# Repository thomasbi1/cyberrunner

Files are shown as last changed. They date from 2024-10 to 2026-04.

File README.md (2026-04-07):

# CyberRunner

CyberRunner (https://youtu.be/zQMKfuWZRdA)

CyberRunner is an AI robot whose task is to learn how to play the popular and widely accessible labyrinth marble game. It is able to beat the best human player with only 6 hours of practice.

This repository contains all necessary code and documentation to build your own CyberRunner robot, and let the robot learn to solve the maze!

**Author: Thomas Bi <br />
With contributions by: Ethan Marot, Tim Flückiger, Cara Koepele, Aswin Ramachandran**

To learn more:
* [Project website](https://cyberrunner.ai)
* [Video](https://youtu.be/zQMKfuWZRdA)
* [Paper](https://arxiv.org/abs/2312.09906)

## Overview

Method

CyberRunner exploits recent advances in model-based reinforcement learning and its ability to make informed decisions about potentially successful behaviors by planning into the future. The robot learns by collecting experience. While playing the game, it captures observations and receives rewards based on its performance, all through the “eyes” of a camera looking down at the labyrinth. A memory is kept of the collected experience. Using this memory, the model-based reinforcement learning algorithm learns how the system behaves, and based on its understanding of the game it recognizes which strategies and behaviors are more promising. Consequently, the way the robot uses the two motors – its “hands” – to play the game is continuously improved. Importantly, the robot does not stop playing to learn; the algorithm runs concurrently with the robot playing the game. As a result, the robot keeps getting better, run after run.

## Documentation

To get started with CyberRunner, please refer to the [Docs](http://cyberrunner.readthedocs.io/).

## Citing
If you use this work in an academic context, please cite the following publication:

* T. Bi, R. D'Andrea,
**"Sample-Efficient Learning to Solve a Real-World Labyrinth Game Using Data-Augmented Model-Based Reinforcement Learning"**, 2024 IEEE International Conference on Robotics and Automation (ICRA). ([PDF](https://arxiv.org/abs/2312.09906))

         @inproceedings{bi2024sample,
          title={Sample-efficient learning to solve a real-world labyrinth game using data-augmented model-based reinforcement learning},
          author={Bi, Thomas and D’Andrea, Raffaello},
          booktitle={2024 IEEE International Conference on Robotics and Automation (ICRA)},
          pages={7455--7460},
          year={2024},
          organization={IEEE}
        }

## License
The source code is released under an [AGPL-3.0 license](LICENSE).

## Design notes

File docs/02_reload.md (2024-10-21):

Reload Mechanism
=====

!!! note

    This page is a work in progress.

> Below are the instructions to add an automatic reload mechanism to the CyberRunner robot. The reload mechanism uses a light sensor to detect when the marble is ready to be reset to the beginning. A solenoid then launches the ball through a tube path back to the start.

## Tools
* Toolkit with Allen wrenches and screwdrivers
* Soldering iron
* Wire clippers and strippers
* Hot glue gun
* Heat gun or hair dryer
* Pliers

## List of Purchased Components
* 1x <a href="https://www.adafruit.com/product/413" target="_blank">Adafruit Large Push-Pull Solenoid</a> 
* 1x <a href="https://store.arduino.cc/products/arduino-nano" target="_blank">Arduino Nano</a>
* 1x <a href="https://www.adafruit.com/product/4681" target="_blank"> Adafruit BH1750 Light Sensor</a>
* 1x <a href="https://www.pololu.com/product/2804" target="_blank">Polulu RC Relay Switch</a>
* 1x <a href="https://www.galaxus.ch/en/s14/product/lumina-swiss-power-supply-dc24v-3a-lighting-accessories-21674974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" target="_blank">DC 24V 3A Power Supply</a> (Example)
* 1x White LED
* 1x 330 Ohm Resistor
* <a href="https://www.adafruit.com/product/793" target="_blank">F/F Jumper Cables</a> (Example)
* 9x M3x8 bolts 
* 6x M3x12 bolts
* 4x M2x16 bolts
* 4x M2 nuts
* Heat shrink
* Optional: Barrel jack adapter to power the solenoid

## List of 3D-Printed Components
* 4x <a href="https://github.com/thomasbi1/cyberrunner/blob/master/docs/assets/reload/reload_leg.step" target="_blank">Labyrinth Legs</a> 
* 1x <a href="https://github.com/thomasbi1/cyberrunner/blob/master/docs/assets/reload/reload_solenoid_push_head.step" target="_blank">Solenoid Push Head Cover</a>
* 1x <a href="https://github.com/thomasbi1/cyberrunner/blob/master/docs/assets/reload/solenoid_sensor_mount.step" target="_blank">Reload Marble Tray - Part 1</a> 
* 1x <a href="https://github.com/thomasbi1/cyberrunner/blob/master/docs/assets/reload/reload_sensor_cover_2.step" target="_blank">Sensor Cover - Part 2</a> 
* 1x <a href="https://github.com/thomasbi1/cyberrunner/blob/master/docs/assets/reload/reload_corridor_3.step" target="_blank">Corridor after Solenoid - Part 3</a> 
* 1x <a href="https://github.com/thomasbi1/cyberrunner/blob/master/docs/assets/reload/reload_corridor_4.step" target="_blank">Corridor - Part 4</a> 
* 1x <a href="https://github.com/thomasbi1/cyberrunner/blob/master/docs/assets/reload/reload_corridor_5.step" target="_blank">Corridor - Part 5</a> 
* 1x <a href="https://github.com/thomasbi1/cyberrunner/blob/master/docs/assets/reload/reload_4_5_mount_6.step" target="_blank">Corridor Mount between 4 and 5 - Part 6</a> 
* 1x <a href="https://github.com/thomasbi1/cyberrunner/blob/master/docs/assets/reload/reload_corridor_7.step" target="_blank">Corridor - Part 7</a> 
* 1x <a href="https://github.com/thomasbi1/cyberrunner/blob/master/docs/assets/reload/reload_corridor_8.step" target="_blank">Corridor - Part 8</a> 
* 1x <a href="https://github.com/thomasbi1/cyberrunner/blob/master/docs/assets/reload/reload_7_8_mount_9.step" target="_blank">Corridor Mount between 7 and 8 - Part 9</a> 
* 1x <a href="https://github.com/thomasbi1/cyberrunner/blob/master/docs/assets/reload/reload_end_holder.step" target="_blank">Corridor End Mount</a> 
* 1x <a href="https://github.com/thomasbi1/cyberrunner/blob/master/docs/assets/reload/reload_corner_holder.step" target="_blank">Corridor Corner Mount</a>
* 1x <a href="https://github.com/thomasbi1/cyberrunner/blob/master/docs/assets/reload/reload_electronics_mount.step" target="_blank">Electronics Holder</a> 

## Building the Reload Mechanism

1. Remove the marble tray. 
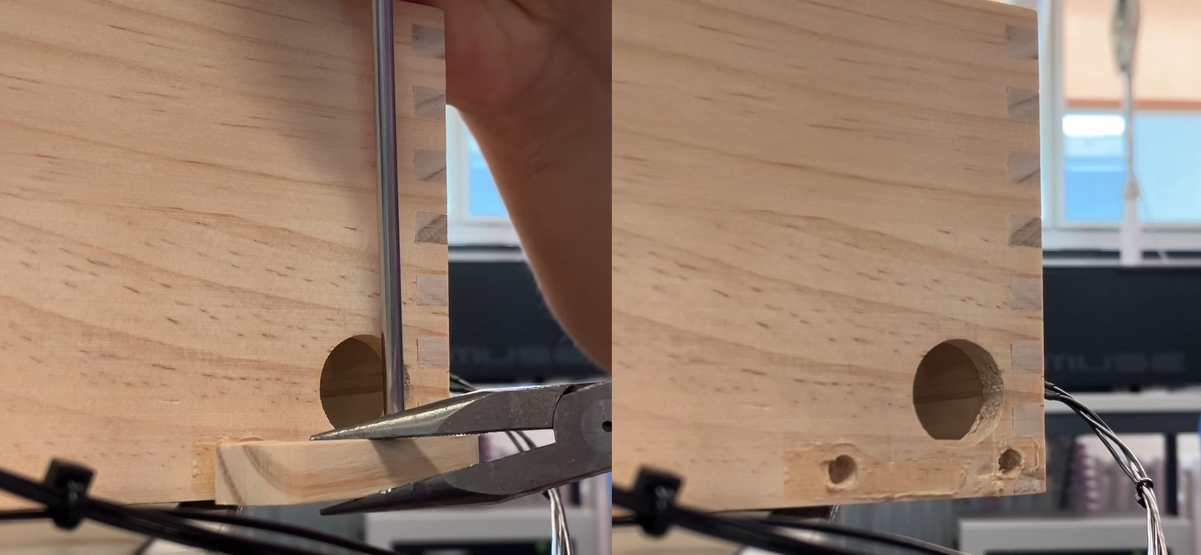
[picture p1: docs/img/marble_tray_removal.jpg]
marble_tray

<br><br>

2. Install the legs on each corner of the labyrinth.

3. Start assembling the new marble tray, which houses the LED, light sensor, and solenoid. Begin with the light sensor and LED wiring. 
    - Solder the pins onto the light sensor PCB facing away from the light sensor. **(Note: This is opposite to the direction shown in the photo)**
    - Solder a 330 Ohm resistor to a (shortened) power lead of the white LED. Solder the other end of the resistor to a female jumper cable. This will connect to the light sensor PCB for power.
    - Create a grounding cable that splits from the (shortened) ground lead of the LED to two female jumper cables. These cables will connect to ground pins on the light sensor PCB and the Arduino.
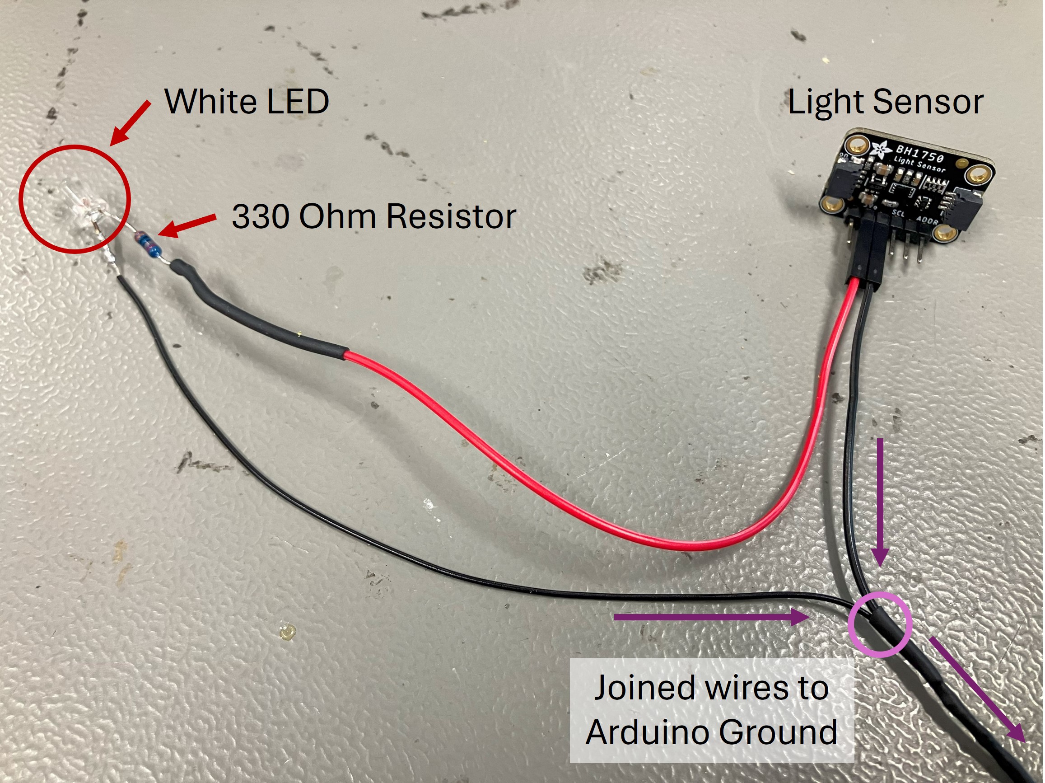
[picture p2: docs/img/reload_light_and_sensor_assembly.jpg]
light_sensor

<br><br>

4. Insert the LED into the designated hole in the printed marble tray. Bend its wires carefully along the corridor so they do not touch each other. Hot glue the wires and the LED in place.<!-- ![knobs](img/marble_tray_removal.jpg) -->
<br><br>

5. Insert the light sensor into its designated spot on the printed marble tray opposite the LED. Install the sensor cover (Part 2).<!-- ![knobs](img/marble_tray_removal.jpg) -->
<br><br>

6. Put the printed cap on the solenoid piston. Attach the solenoid to the printed marble tray using four M3x12 bolts. Ensure the piston faces inward to launch the marble.<!-- ![knobs](img/marble_tray_removal.jpg) -->
<br><br>

7. Secure the reload mechanism assembly to the labyrinth with two M3x8 bolts in the lower right holes of the connection points. <!-- ![knobs](img/marble_tray_removal.jpg) -->
<br><br>

8. Assemble the marble return corridor using the numbered parts:
    - Press-fit Part 3 into the printed marble tray and secure it to the labyrinth with one 3Mx8 bolt. Attach Part 4 to Part 3. 
    - Connect Parts 4 and 5 using Part 6, securing it to the top of the labyrinth with two 3Mx8 bolts. 
    - Press-fit Part 7 to Part 5. Connect Part 7 and Part 8 with Part 9. Secure Part 9 to the top of the labyrinth with two 3Mx8 bolts. 
    - Attach the end mount to Part 8 and secure it above the maze start with two 3Mx8 bolts. 
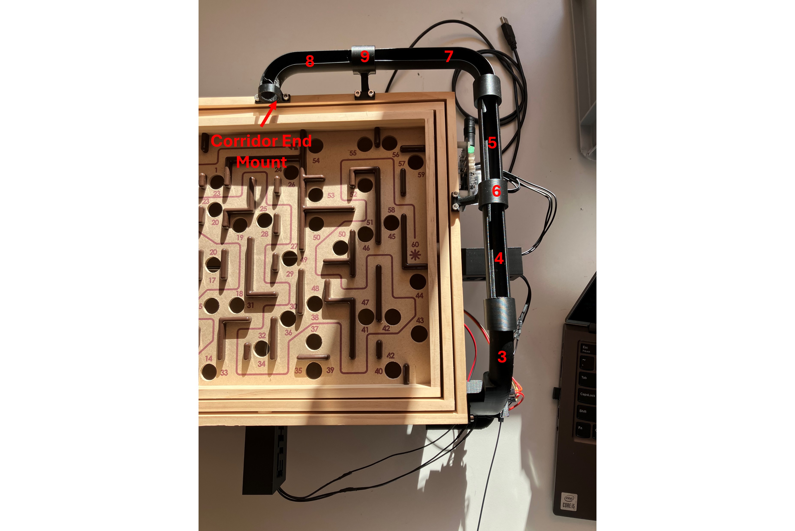
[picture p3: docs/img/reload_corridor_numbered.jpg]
reload_corridor

<br><br>

9. Connect the cables for the light sensor, solenoid, Arduino, and relay according to the wiring diagram. Optionally, connect the solenoid and relay to the 24V power supply using a barrel jack connector in the electronics housing. 
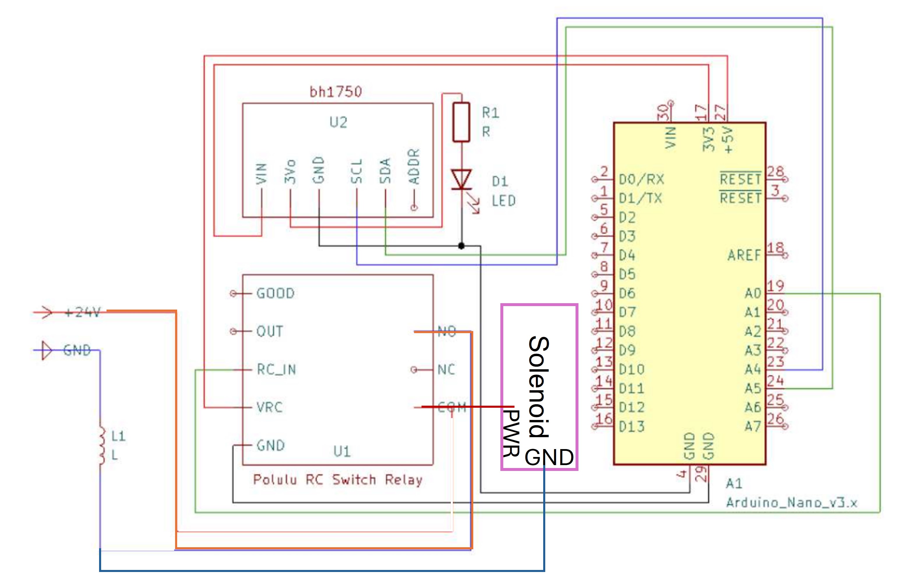
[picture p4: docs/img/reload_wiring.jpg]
reload_wiring

<br><br>

10. Secure the relay in the electronics housing with M2x16 bolts and nuts. Press-fit the Arduino in the leg features. 
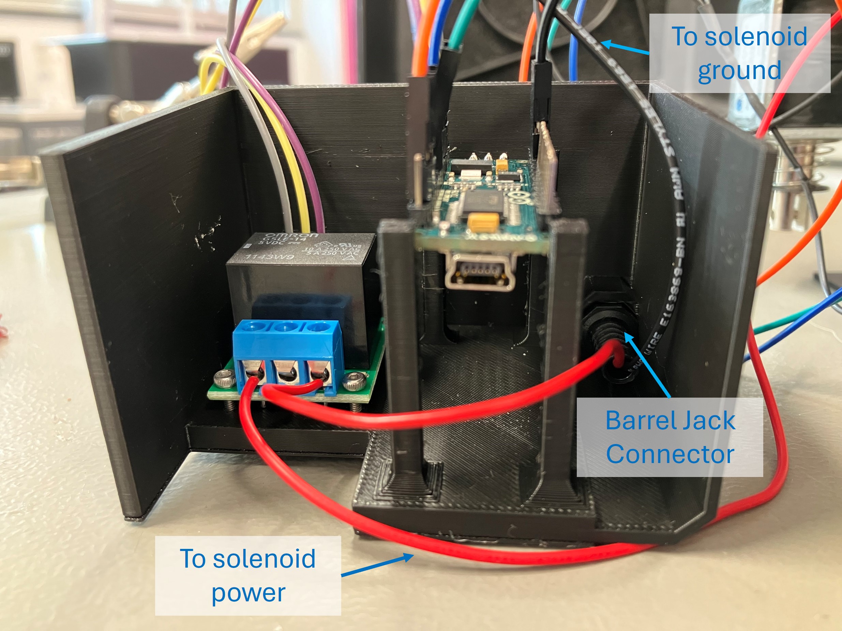
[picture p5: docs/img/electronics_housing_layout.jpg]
housing_layout

<br><br>

11. Attach the housing to the labyrinth with two M3x12 bolts.
<br><br>

## Configuring the Electronics

1. Plug in the Arduino to your PC and upload <a href="https://github.com/thomasbi1/cyberrunner/blob/master/docs/assets/reload/arduino/main.ino" target="_blank">this script</a> to the Arduino Nano. Ensure that the BH1750 library is installed.

2. If the Arduino is powered, you should hear the relay respond when the LED is blocked by the marble. Power the solenoid with the 24V power supply to engage the reload feature!

 <!-- and (2) every 10 minutes without sensor detection. The latter response attempts to jiggle out stuck marbles from the labyrinth. -->

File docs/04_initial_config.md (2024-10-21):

Initial Configuration
=====

Before we can start using CyberRunner, we need to first **calibrate the camera** and **configure the motors**. These steps have to be taken only once. 

## Camera Calibration

In order for the position of the ball within the labyrinth to be tracked, we need to first calibrate the camera. For this purpose, we use the <a href="https://sites.google.com/site/scarabotix/ocamcalib-omnidirectional-camera-calibration-toolbox-for-matlab" target="_blank">COCamCalib MATLAB toolbox</a>.

1. Follow the steps <a href="https://sites.google.com/site/scarabotix/ocamcalib-omnidirectional-camera-calibration-toolbox-for-matlab" target="_blank">here</a> to obtain the calibration results for your camera. 

    !!! warning "Disclaimer"

        The **Find Center** step is computationally intensive and may get stuck. In this case, update `PP` in both instances of the function `lsqlin()` to `sparse(PP)`. This should speed up the process. For more details, the bug fix is idenitified in <a href="https://groups.google.com/g/ocamcalib-toolbox/c/ZgVP4LHd-6w?pli=1" target="_blank">this thread</a>.

    Make sure to take the calibration pictures at a 1920x1200 resolution.

2. Save the calibration results by clicking on **Export Data** in the OCamCalib GUI. This will create the file `calib_results.txt` in your MATLAB workspace.

3. Copy the `calib_results.txt` file as `calib_results_cyberrunner.txt` to your ROS workspace with

        cp <path_to_matlab_workspace>/calib_results.txt <path_to_cyberrunner_ws>/src/cyberrunner/cyberrunner_state_estimation/calib/calib_results_cyberrunner.txt
    Replace `<path_to_matlab_workspace>` and `<path_to_cyberrunner_ws>` with the path to your MATLAB workspace and your CyberRunner ROS workspace, respectively.

4. Install the calibration file by navigating to your workspace and running

        colcon build --symlink-install
        source install/setup.bash

## Marker positions

The state estimator relies on approximately knowing the location of the blue markers within the image. To obtain these positions follow these steps.

1. Open two terminal windows, navigate to the CyberRunner workspace and source the workspace.

2. In the first terminal, run the camera script

        ros2 run cyberrunner_camera cam_publisher.py

3. In the second terminal, run the select markers script and follow the instructions in the terminal

        ros2 run cyberrunner_state_estimation select_markers

## Motor Configuration

1. Install [Dynamixel Wizard 2.0](https://emanual.robotis.com/docs/en/software/dynamixel/dynamixel_wizard2/).
2. Temporarily disconnect the front motor (the motor on the longer side of the labyrinth). Connect the U2D2 to your host PC and ensure that the motors are turned on by pressing the power switch on the U2D2 Power Hub Board.
3. In the Dynamixel Wizard, press **Scan** until the motor is found.
4. Assign **ID 2** to the connected motor, set the baud rate to 1M, and set the operating mode to 0 (Current Control Mode). Make sure to click **Save** after each change.
5. Reconnect the front motor.
6. Press **Scan** again.
7. For the newly connected motor, assign **ID 1**, and apply the same changes as for the other motor.

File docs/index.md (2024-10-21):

# CyberRunner Documentation

Welcome to the CyberRunner docs! Here you'll find tutorials and other useful information to get you started with CyberRunner.

## Requirements

* Ubuntu 22.04
* MATLAB
* GPU: min. 1x RTX 2080 Super

## Tutorials

* [Hardware Setup](01_hardware_setup.md): Build your own CyberRunner robot.
* [Reload Mechanism](02_reload.md): Add an automatic reload mechanism to your CyberRunner robot.
* [Installation](03_installation.md): Install all necessary dependencies and the CyberRunner software stack.
* [Initial Configuration](04_initial_config.md): Calibrate the camera and configure the motors.
* [Train](05_train.md): Let CyberRunner learn to play the labyrinth game.
* [Troubleshooting](06_troubleshooting.md): Fix common issues.

!!! note "Note"

    This project is under active development.

<!-- !!! Potential addition

    Video tutorials? This applies to software and configuration as well -->

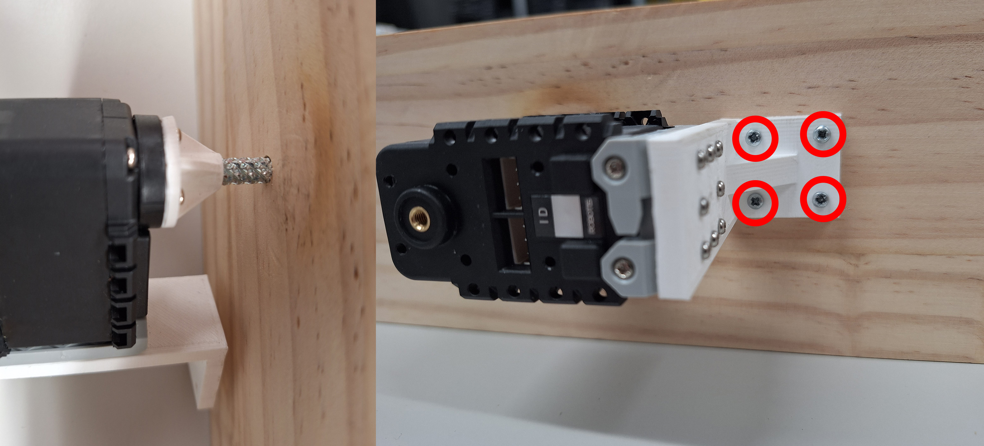
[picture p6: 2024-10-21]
docs/img/motorfix.jpg

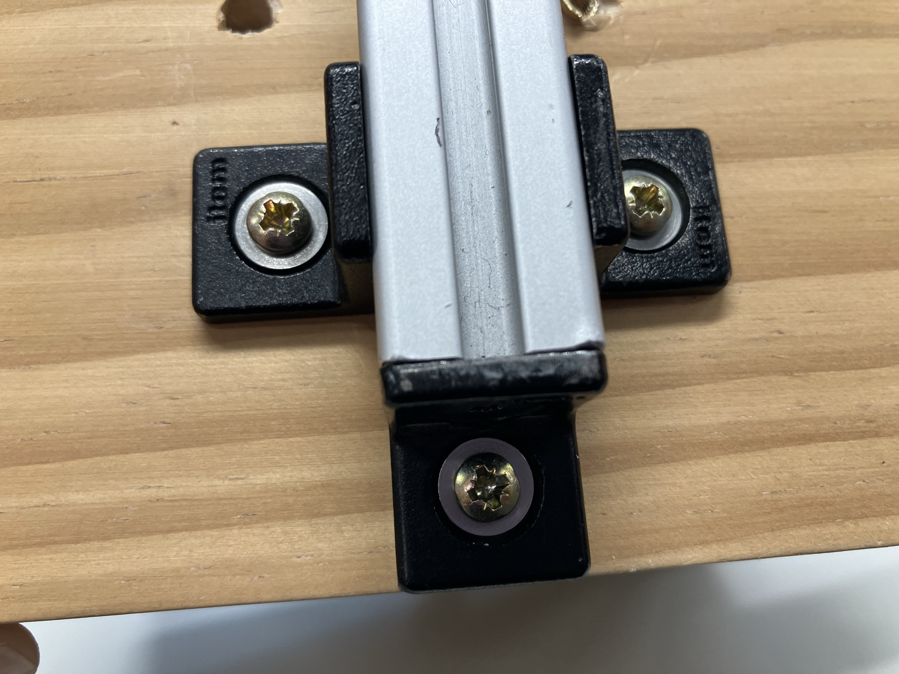
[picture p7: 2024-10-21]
docs/img/camera_scaffolding_to_labyrinth.jpg

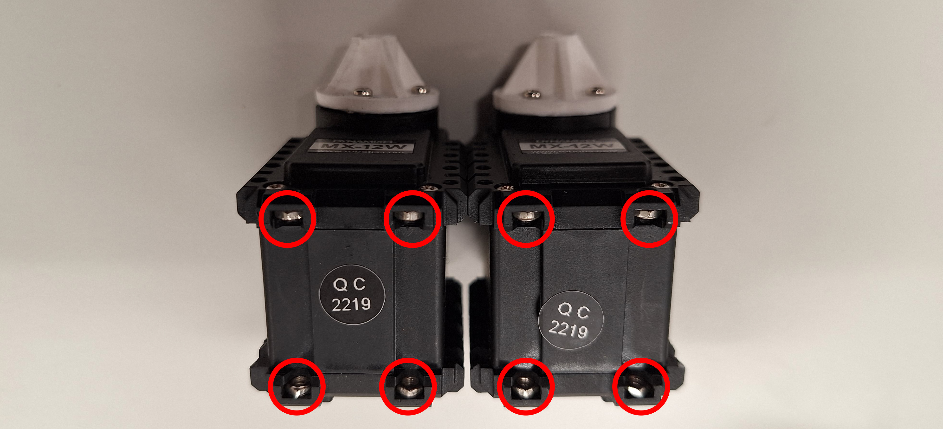
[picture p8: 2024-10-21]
docs/img/nuts.jpg

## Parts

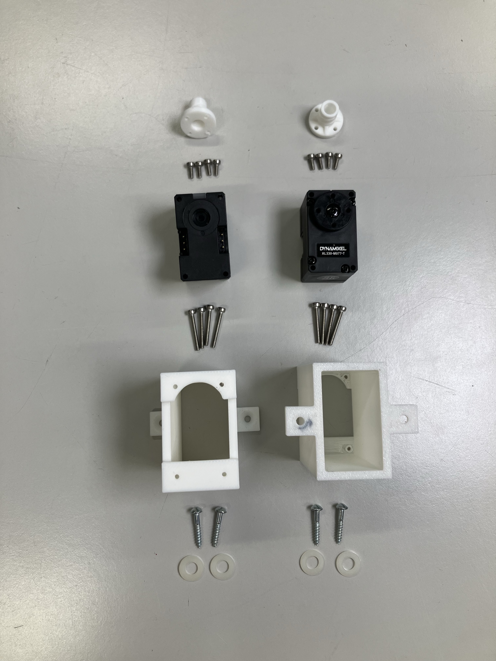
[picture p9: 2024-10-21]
docs/img/motor_housing_parts.jpg

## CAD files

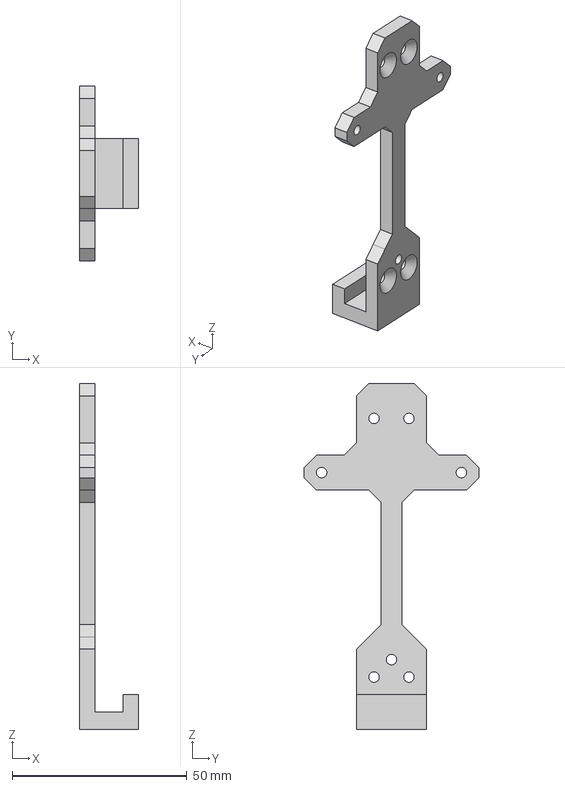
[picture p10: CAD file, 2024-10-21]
docs/assets/camera/camera_assembly_mount.step
17.0 x 50.0 x 99.0 mm

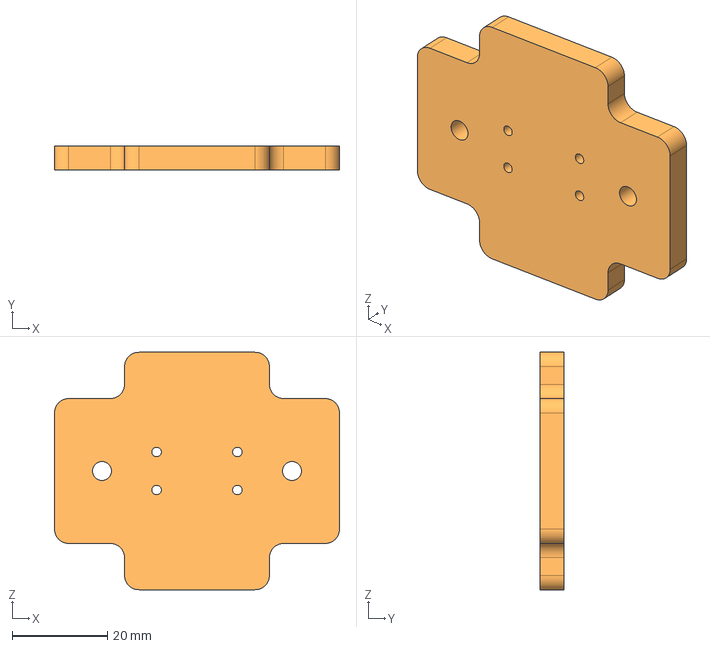
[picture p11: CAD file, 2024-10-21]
docs/assets/camera/camera_mounting_plate.step
60.0 x 5.00 x 50.0 mm

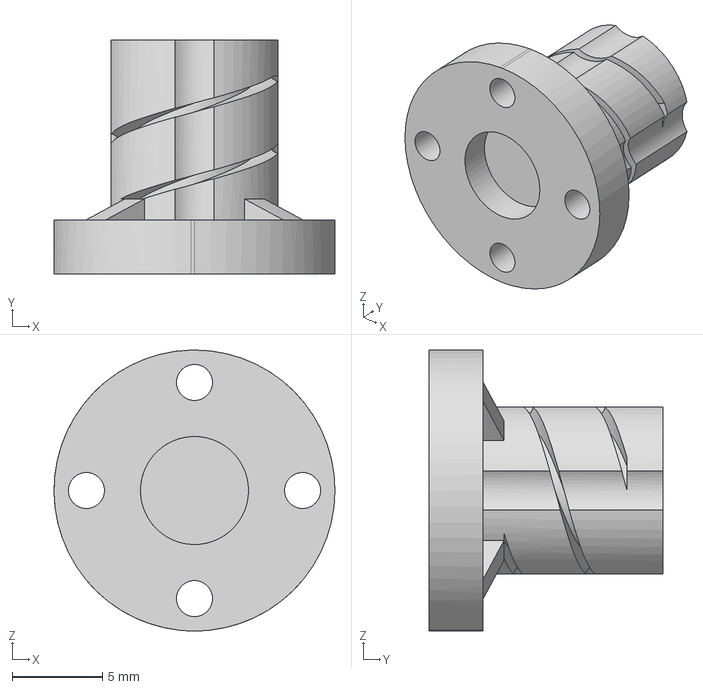
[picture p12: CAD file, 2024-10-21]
docs/assets/motors/motor_shaft_coupler.step
15.6 x 13.0 x 15.6 mm

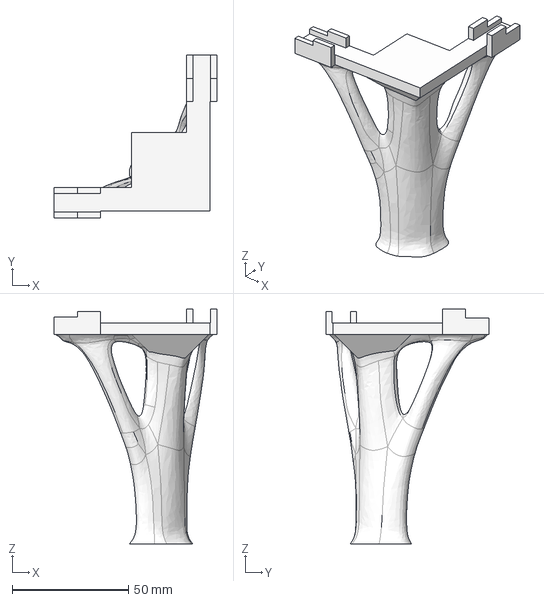
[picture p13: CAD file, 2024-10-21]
docs/assets/reload/reload_leg.step
70.0 x 70.0 x 101.0 mm

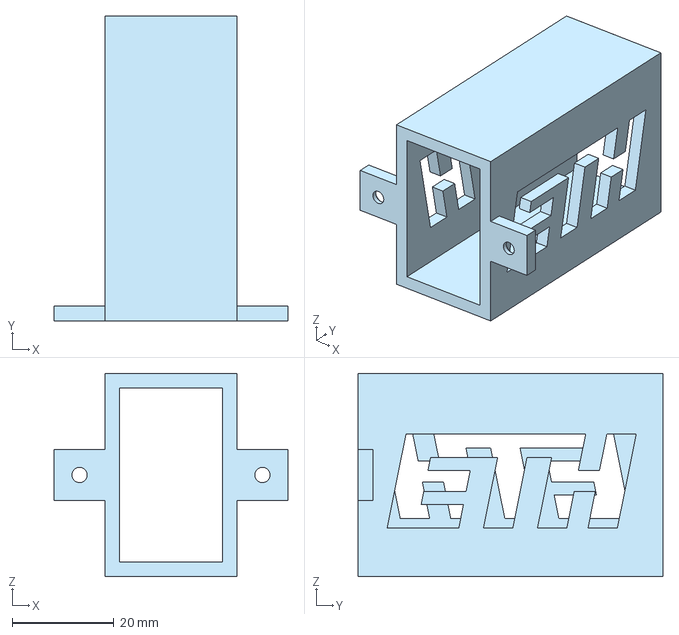
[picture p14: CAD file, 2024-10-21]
docs/assets/motors/motor_mounting_bracket.step
46.0 x 60.0 x 40.0 mm

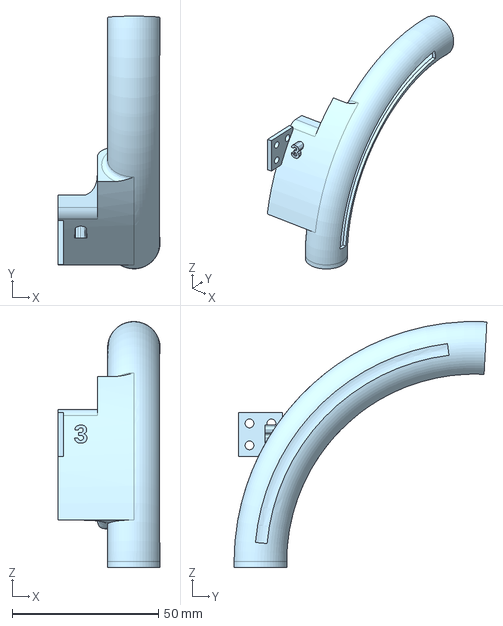
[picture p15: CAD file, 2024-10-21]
docs/assets/reload/reload_corridor_3.step
35.0 x 86.4 x 84.1 mm

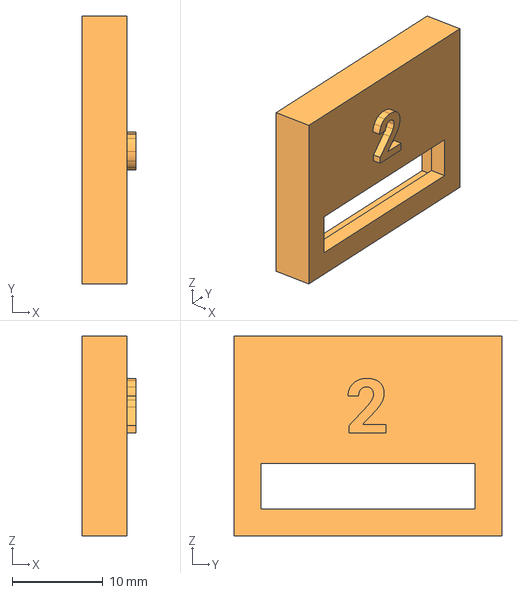
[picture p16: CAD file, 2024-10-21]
docs/assets/reload/reload_sensor_cover_2.step
6.00 x 29.6 x 22.1 mm

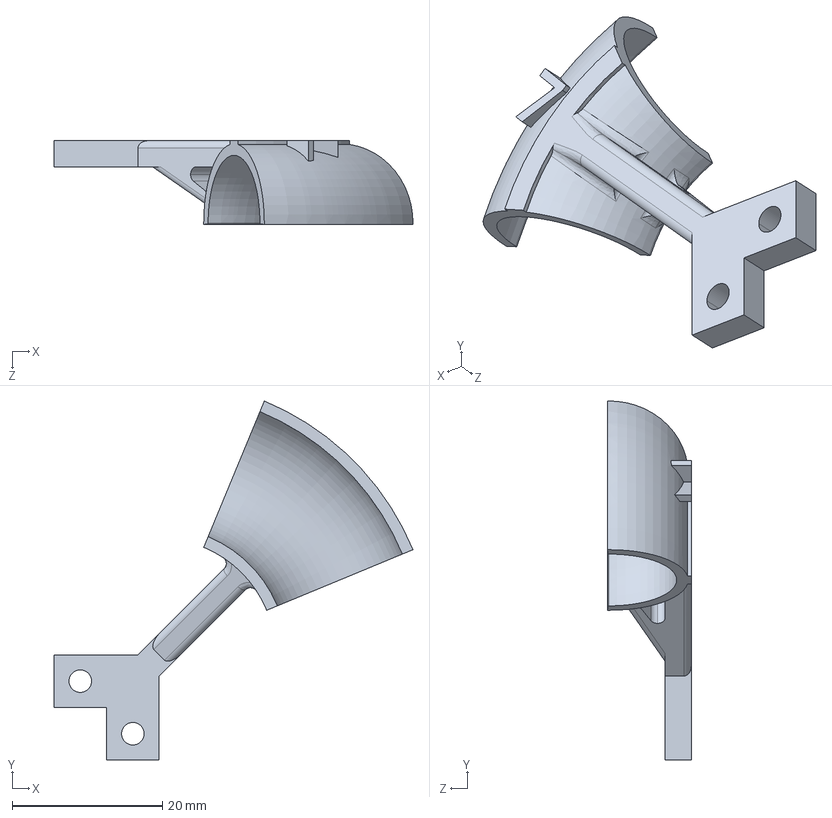
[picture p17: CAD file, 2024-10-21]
docs/assets/reload/reload_corner_holder.step
47.8 x 47.8 x 11.1 mm

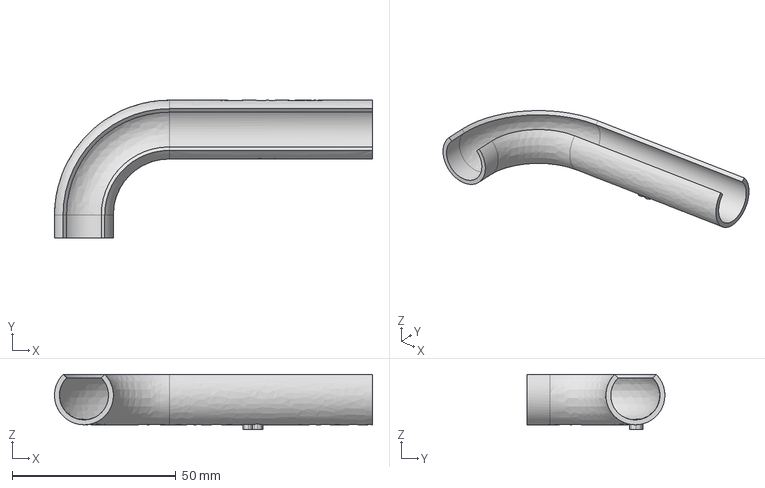
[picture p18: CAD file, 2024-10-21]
docs/assets/reload/reload_corridor_8.step
97.0 x 42.0 x 16.8 mm

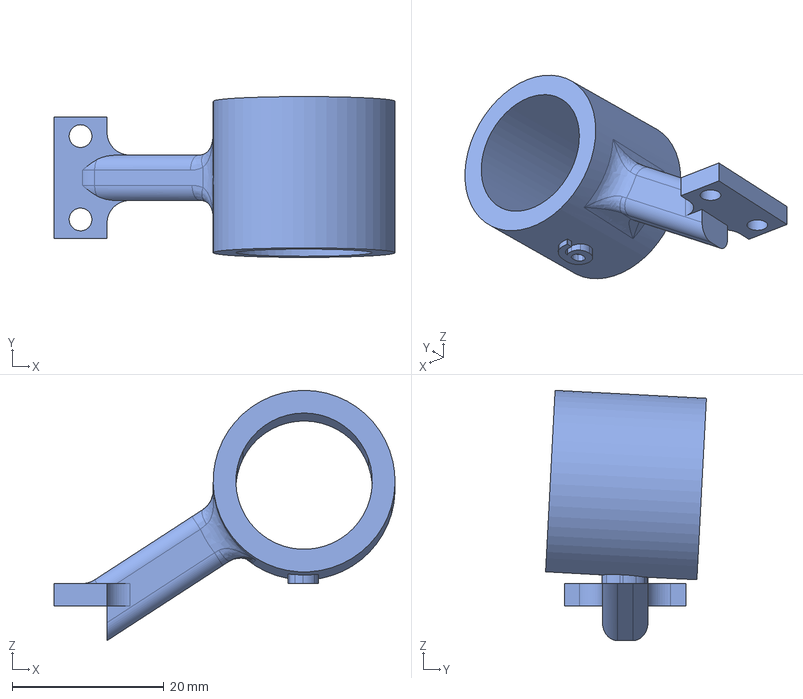
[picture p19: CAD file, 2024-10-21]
docs/assets/reload/reload_4_5_mount_6.step
45.0 x 21.2 x 33.0 mm

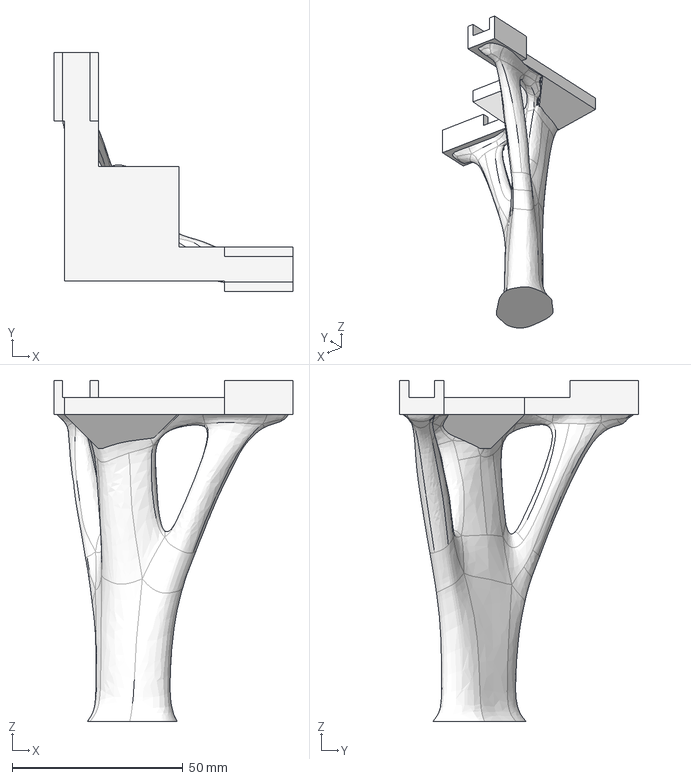
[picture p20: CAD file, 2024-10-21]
docs/assets/reload/reload_leg_electronics.step
70.0 x 70.0 x 100.0 mm

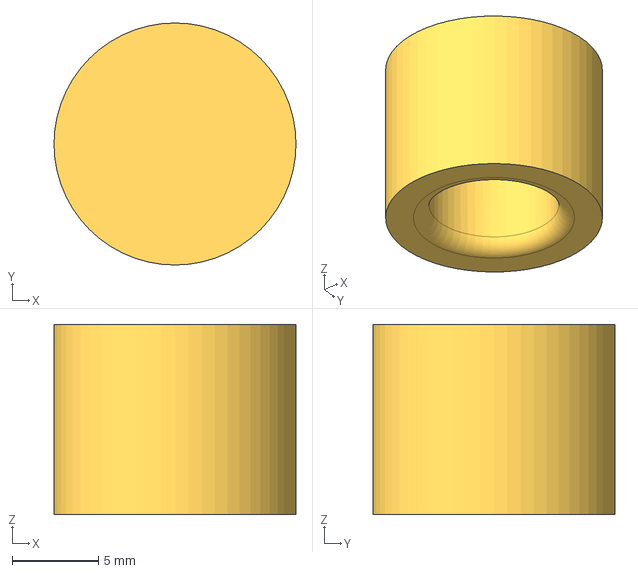
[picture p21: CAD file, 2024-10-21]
docs/assets/reload/reload_solenoid_push_head.step
14.0 x 14.0 x 11.0 mm

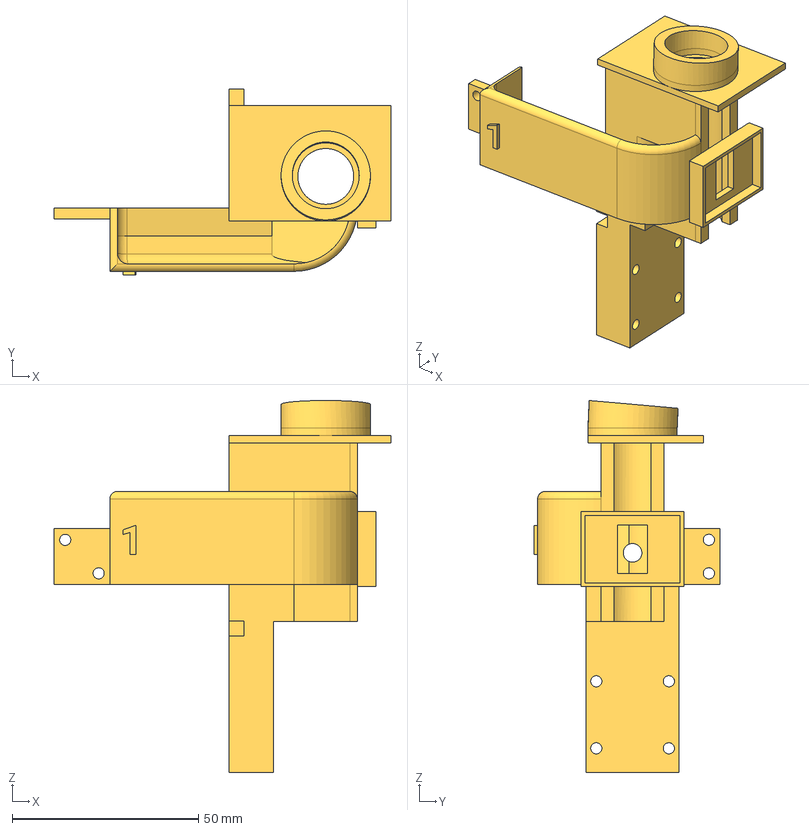
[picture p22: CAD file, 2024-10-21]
docs/assets/reload/solenoid_sensor_mount.step
90.5 x 50.0 x 99.9 mm

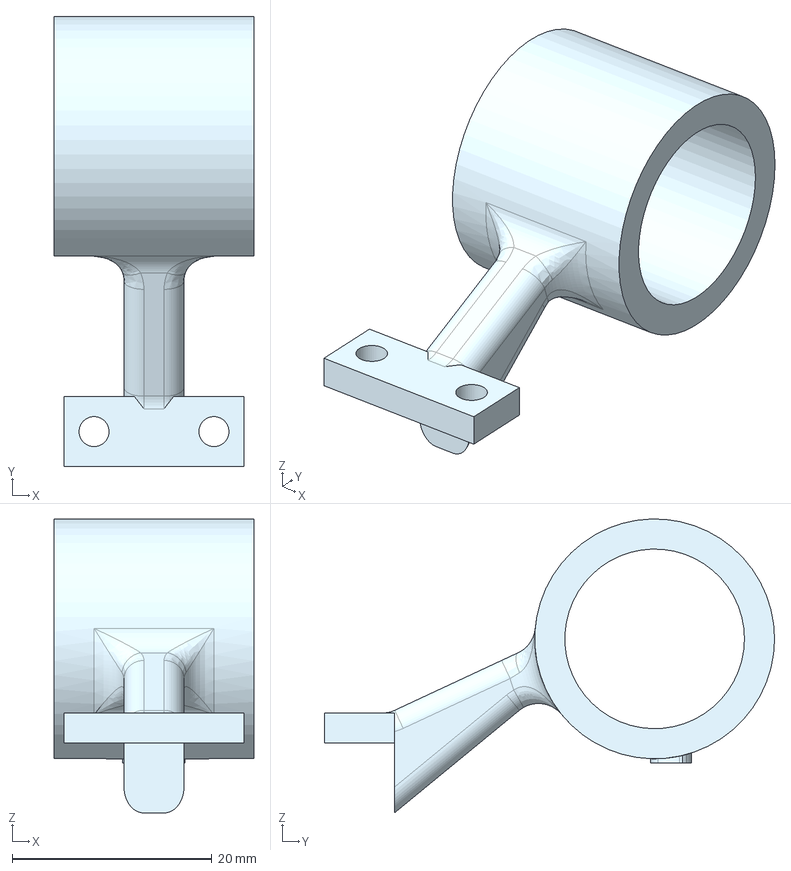
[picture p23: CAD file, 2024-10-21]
docs/assets/reload/reload_7_8_mount_9.step
20.0 x 45.0 x 29.4 mm

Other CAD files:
docs/assets/reload/reload_corridor_4.step
docs/assets/reload/reload_end_holder.step
docs/assets/reload/reload_corridor_5.step
docs/assets/reload/reload_corridor_7.step
docs/assets/reload/reload_brightness_cover.step
docs/assets/reload/reload_electronics_mount.step

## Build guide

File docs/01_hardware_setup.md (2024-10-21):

Hardware Setup
=====

## List of Components

### Tools
* 3D-Printer access and PLC filament (Tested with Bambu X1E)
* Toolkit with Allen wrenches, screwdrivers, and a handheld drill
* Wire cutters and strippers
* Soldering iron
* Heat gun or hair dryer
* Pliers

### Labyrinth
<!-- * 1x [BRIO Labyrinth](https://www.brio.us/en-US/products/games/labyrinth-game-63400000) (wooden version) -->
* 1x <a href="https://www.brio.us/en-US/products/games/labyrinth-game-63400000" target="_blank">BRIO Labyrinth</a> (wooden version)

### XL330-M077-T Motors 
* 2x <a href="https://www.robotis.us/dynamixel-xl330-m077-t/" target="_blank">ROBOTIS Dynamixel XL330-M077-T</a>
* 1x <a href="https://www.robotis.us/u2d2/" target="_blank">ROBOTIS U2D2</a>
* 1x <a href="https://www.robotis.us/u2d2-power-hub-board-set/" target="_blank">ROBOTIS U2D2 Power Hub Board</a>
* 3x wires to extend cable to reach between both motors
* 1x 5V3A Power Supply (2.5mm ID / 5.5mm OD) - <a href="https://www.amazon.com/Supply-Adapter-100-240V-Replacement-Transformer/dp/B0B524GZMN" target="_blank">example</a>
* 2x <a href="https://github.com/thomasbi1/cyberrunner/blob/master/docs/assets/motors/motor_shaft_coupler.step" target="_blank">Motor couplings</a> (to 3d print)
    Note: These couplings may break after being coupled to the motor. We recommend to print 2x extra.
* 2x <a href="https://github.com/thomasbi1/cyberrunner/blob/master/docs/assets/motors/motor_mounting_bracket.step" target="_blank">Motor mounting brackets</a> (to 3d print)
* 8x M2x6 B610 bolts fix couplers to the motors (included with motors)
* 4x M3x10 bolts to mount bracket to the labyrinth
* Heat shrink

### Camera
* 1x <a href="https://www.e-consystems.com/industrial-cameras/ar0234-usb3-global-shutter-camera.asp#" target="_blank">See3CAM_24CUG USB3 Camera</a> (with enclosure)
* 1x <a href="https://github.com/thomasbi1/cyberrunner/blob/master/docs/assets/camera/camera_mounting_plate.step" target="_blank">Camera mounting plate</a> 
* 1x <a href="https://github.com/thomasbi1/cyberrunner/blob/master/docs/assets/camera/camera_assembly_mount.step" target="_blank">Camera assembly bracket</a>
* 4x M2x8 bolts to attach the camera to the mounting plate
* 2x 2020 T-slotted Aluminum with lengths of 40 cm and 20 cm
* 7x L-brackets for T-slotted aluminum, size M5
* 9x T-slot nuts, size M5
* 9x T-slot bolts, size M5x8
* 2x T-slot bolts, size M4x10, to attach the mounting plate to the L-brackets
* 4x M2.5x10 bolts to attach the assembly bracket to the labyrinth
* 3x M3x8 bolts to mount the camera assembly to the bracket on the labyrinth
* 3x M3 washers to sit between the bolts and the L-brackets that attach to the assembly bracket

!!! note "Information"
    One of the ends of the 40 cm T-slotted aluminum parts needs to be tapped for an M5 bolt. 

### Miscellaneous
* 8x <a href="https://www.herma.co.uk/office-home/product/colour-dots-small-pack-1833/" target="_blank">Dark blue circle labels</a> (8mm diameter)
* 1x <a href="https://www.amazon.com/Ravensburger-27468-GraviTrax-Ball-Box/dp/B0BSX781QZ" target="_blank">Blue colored marbles</a>

## Building CyberRunner

###  XL330-M077-T Motors

1. Using a flathead screwdriver, carefully pry the two knobs off of the labyrinth. Applying heat to the knobs with a heat gun or hair dryer will facilitate this process.
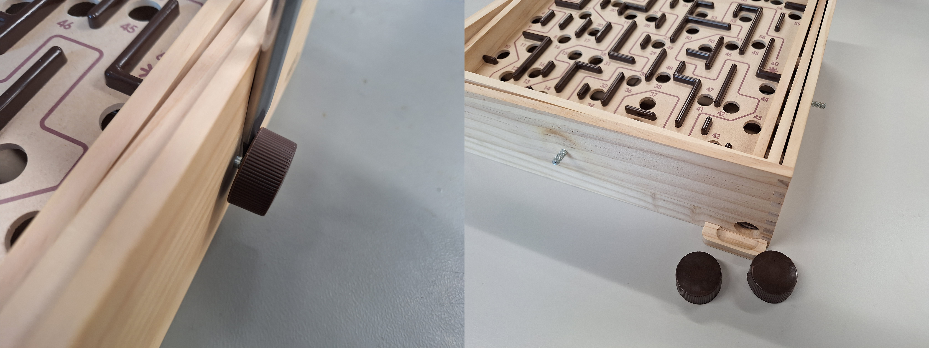
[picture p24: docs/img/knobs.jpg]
knobs

<br><br>

2. Secure the motor couplers to the motors using the provided M2x6 bolts.
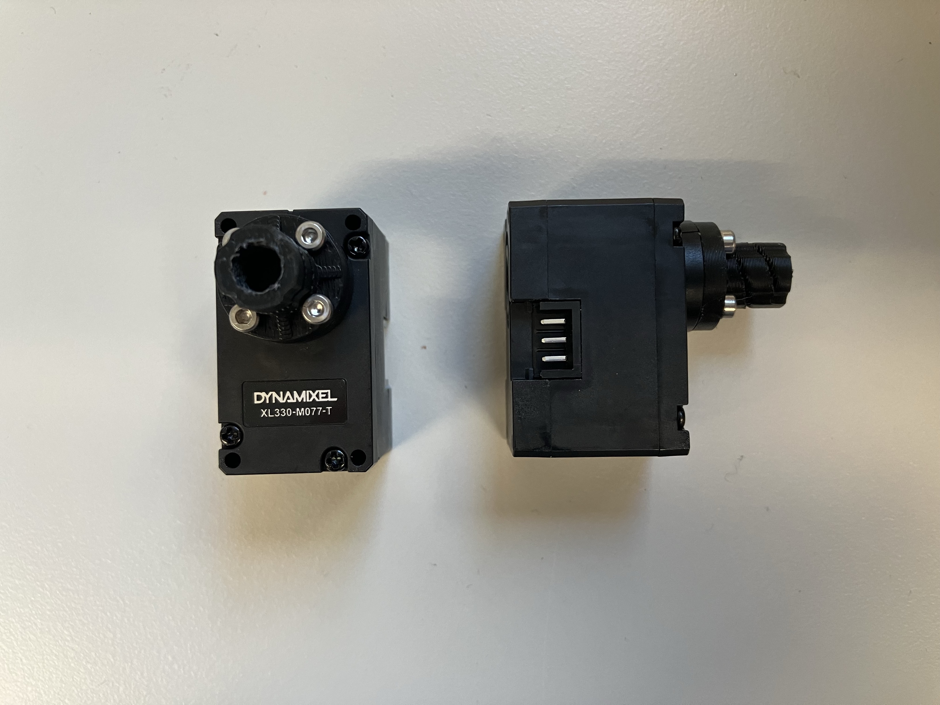
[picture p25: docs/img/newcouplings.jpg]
newcouplers

<br><br>

3. Drill pilot holes on the labyrinth to prepare for the installation of the motor housings. 
<br><br>

4. Connect the motors to the labyrinth shafts. If necessary, slightly heat the couplers with a heat gun or hair dryer to assist with the fitting. Slide the 3D-printed housings over the motors and secure the motor housings to the labyrinth with the M3x10 bolts.
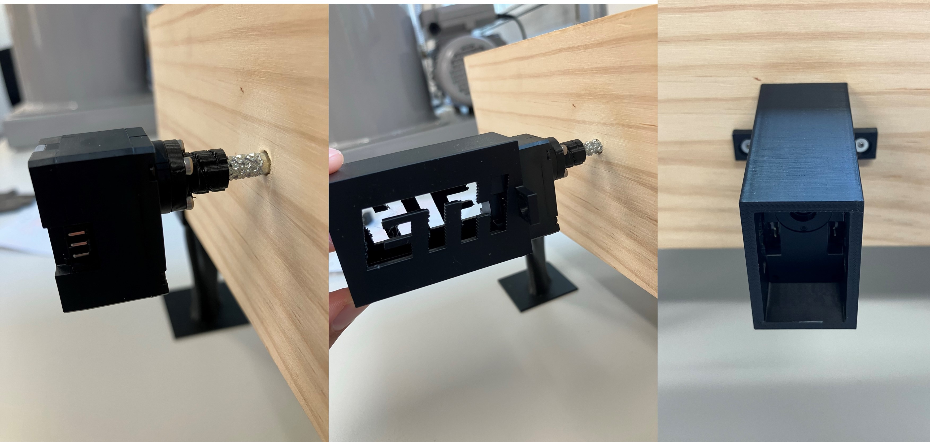
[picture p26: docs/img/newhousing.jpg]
newnuts

<br><br>

<!-- ###  MX-12W Motors (Option 2)

!!! warning "Disclaimer"

    The Dynamixel MX-12W motors have been discontinued. Instructions for the Dynamizel XL330-M077-T motors are above.

1. Carefully remove the two knobs from the labyrinth by using a flathead screwdriver and pressing the knobs away from the labyrinth board. Slightly heating the knobs with a heat gun or a hairdryer will facilitate this process.
![knobs](img/knobs.jpg)
<br><br>

2. Mount the motor couplers to the front of the motors using the M2x6 bolts included with the motors.
![couplers](img/couplers.jpg)
<br><br>

3. Insert the included nuts on the underside of the motors.
![nuts](img/nuts.jpg)
<br><br>

4. Mount the included mounting frames of the motors to the 3d-printed mounting brackets using the included M2x6 bolts and nuts.
![brackets](img/brackets.jpg)
<br><br>

5. Attach the motors to the mounting frames using the included M2x6 bolts.
![motorframe](img/motorframe.jpg)
<br><br>

6. Press both motor couplers over the labyrinth shafts. You may need to slightly heat the couplers with a heat gun or hairdryer. Then, fix the motors to the labyrinth by using the M2.5x10 wood screws.
![motorfix](img/motorfix.jpg) -->

### Camera

The camera has to be have a stable view of the whole labyrinth. This can be done with a scaffolding made with 2020 T-slotted Aluminum and a 3D-Printed camera mounting plate as described below.
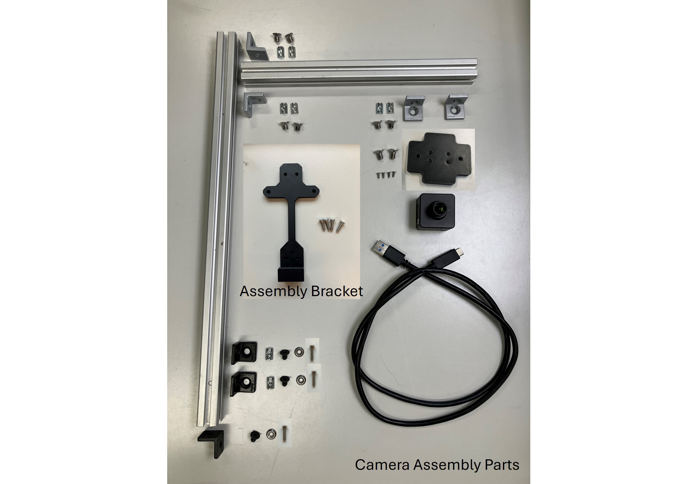
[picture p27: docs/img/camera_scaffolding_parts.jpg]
cameraparts


1. Tap one end of the 40 cm T-slotted aluminum to fit a M5 bolt. Mount the camera to the mounting plate with four M2x8 bolts and assmble the aluminum profiles as shown in the picture.  
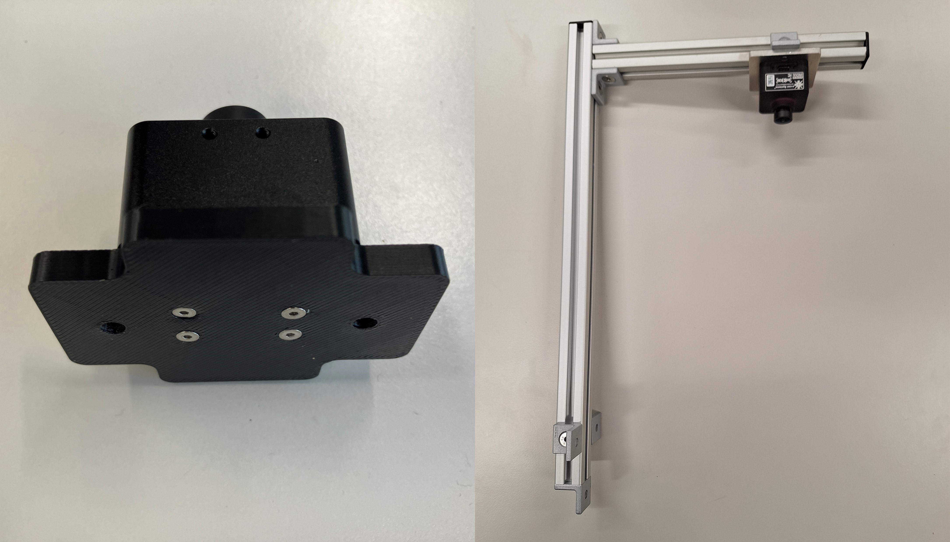
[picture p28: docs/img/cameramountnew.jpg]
cameramount

<br><br>

2. Secure the camera assembly bracket to the labyrinth using four M2.5x10 bolts. Ensure that the bracket is centered. Note that the shaft for the knob on the opposite end is not centered with respect to the playing area.
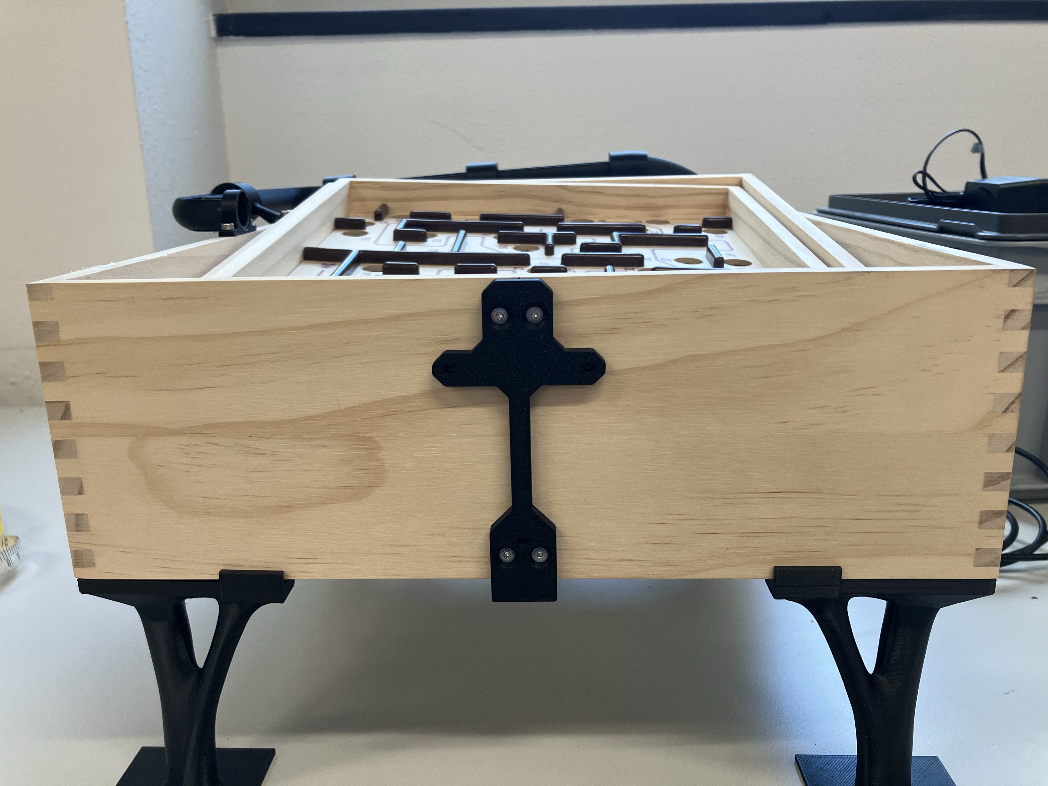
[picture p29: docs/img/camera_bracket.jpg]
camerabracket

<br><br>

3. Mount the camera assembly to the labyrinth board using three M3x8 bolts and M3 washers. Adjust the height of the camera so the distance between the bottom of the lens and the labyrinth playing area is approximately 25cm.
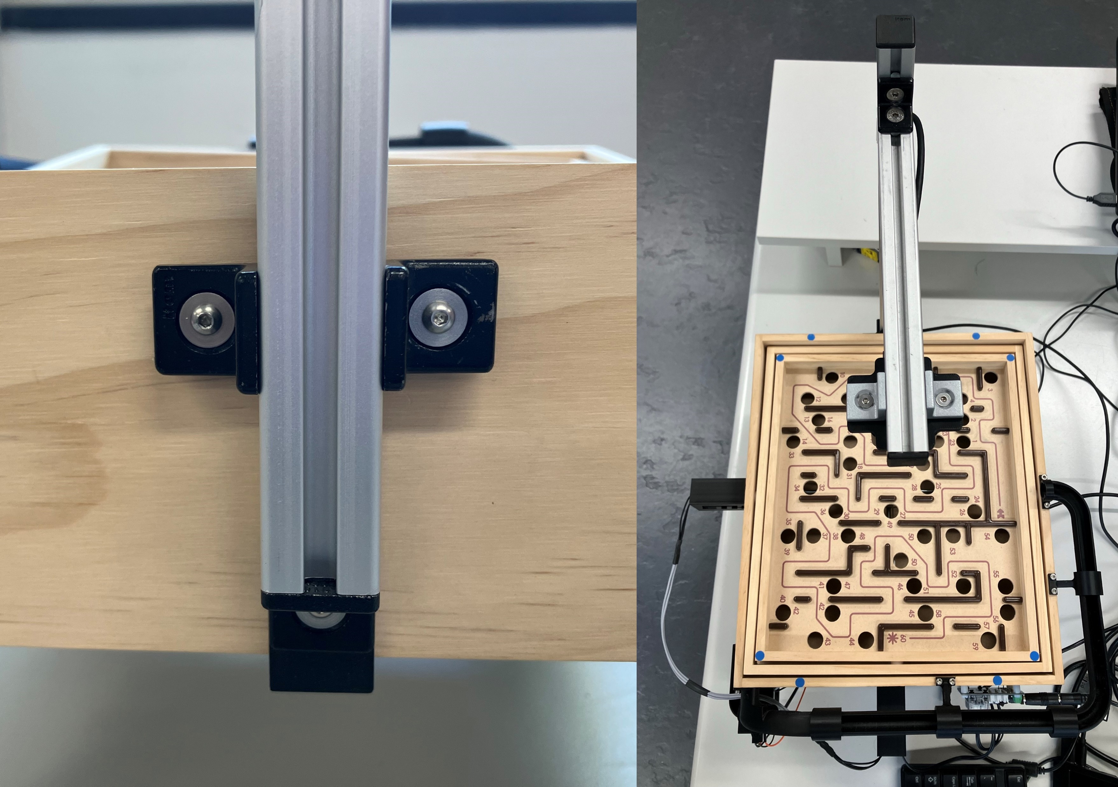
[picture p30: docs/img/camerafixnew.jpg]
camerafix
 

<!-- !!! Warning

    Ensure that the wood screws do not interfere with the motion of the labyrinth playing surface!(TODO photo - also update photo with correct side of labyrinth) -->

### Calibration Markers

Next, blue markers are placed on the labyrinth to estimate the inclination angles of the labyrinth playing surface.

1. Place the first four blue labels on the center of each corners of the inner labyrinth playing surface. The labels should align with the outer edges since the diameter of the labels and the width of the edge are both 8mm. 
<br><br>
2. Place the next four blue labels on the outer perimeter of the labyrinth. The centers of each label should be 5cm from the inner edge of the external enclosure of the game along the short sides of the labyrinth, as shown in the image below.
<br><br>
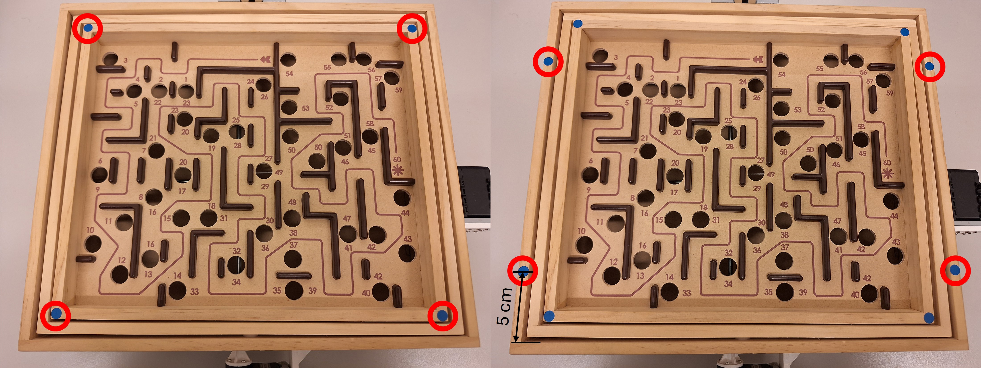
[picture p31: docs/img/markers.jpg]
markers


### Cabling

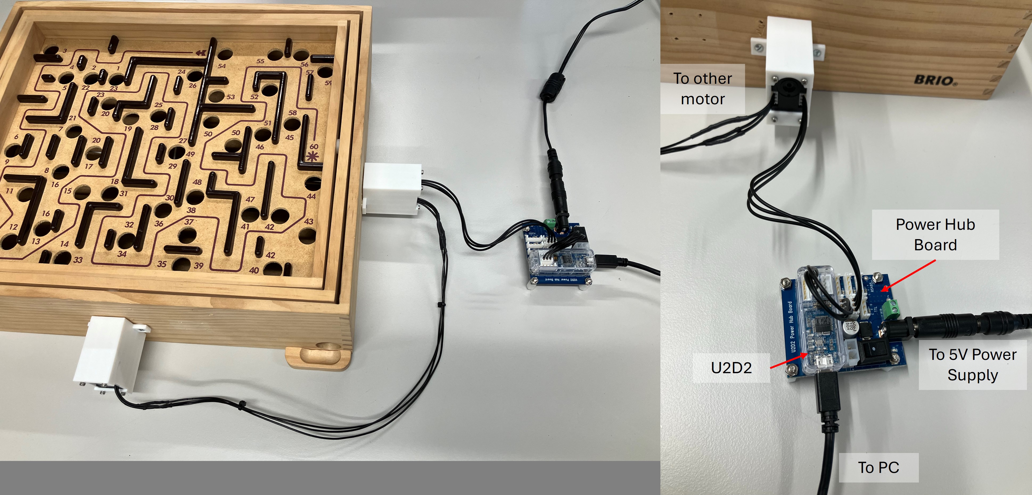
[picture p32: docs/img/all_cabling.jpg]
allcables


1. Clip the ends of two ROBOT X3P cables. Add extra wire between the corresponding pins and solder the connections. Cover the connections with heat shrink.
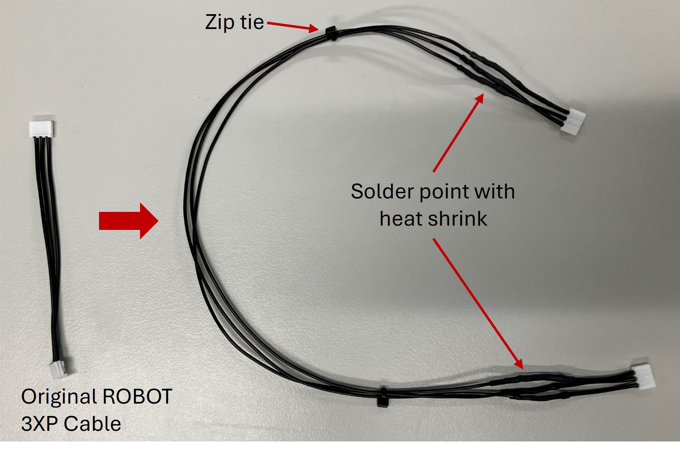
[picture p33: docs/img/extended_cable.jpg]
extendedcable

<br><br>

2. Use the extended ROBOT X3P cable to connect the motors together. Connect the motor opposite the camera scaffolding to the U2D2 with the ROBOT X3P cable from the Starter Kit. Connect the U2D2 to the Power Hub with another ROBOT X3P cable. See the <a href="https://emanual.robotis.com/docs/en/parts/interface/u2d2_power_hub/" target="_blank">U2D2 Power Hub Manual</a> for more information.

3. The U2D2 communicates the computed actions from the computer to the motors. Connect it to the computer with the USB Micro-B cable provided in the Starter Kit.

4. Connect the camera to the computer with the included USB cable.

4. Plug in the 5V Power Supply and connect it to the U2D2 Power Hub to power the motors.

!!! warning "Warning"

    The power supply in the Starter Kit is 12 V and should not be with these motors!

5. OPTIONAL: Use the included rivets and supports to secure the U2D2 and Power Hub to the side or bottom of the labyrinth. If desired, organize the cables with zip ties and zip tie mounts. 
<!-- (TODO photo) -->

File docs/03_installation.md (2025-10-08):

Installation
=====

1. Install [ros2-humble](https://docs.ros.org/en/humble/Installation/Ubuntu-Install-Debians.html) by following the instructions on the linked page. Afterward, complete the [CLI-Configuring-Environment](https://docs.ros.org/en/humble/Tutorials/Beginner-CLI-Tools/Configuring-ROS2-Environment.html) tutorial to source your setup files.

2. Create your ROS2 workspace.

        mkdir cyberrunner_ws && cd cyberrunner_ws && mkdir src && cd src

3. Clone this repository into your ROS2 workspace and navigate back to the workspace root.

        git clone https://github.com/thomasbi1/cyberrunner.git
        cd ..

4. Install [jax](https://jax.readthedocs.io/en/latest/installation.html) with GPU support.

        pip install --upgrade "jax[cuda12_pip]" -f https://storage.googleapis.com/jax-releases/jax_cuda_releases.html

5. Install dreamerv3. NB: The current version of `dreamerv3` requires `gym==0.19.0`, which is not supported by `pip>=24.1`. `pip` must be downgraded to install `dreamerv3`.

        pip install --upgrade pip==24.0
        pip install -e src/cyberrunner/dreamerv3

    Optional: To revert `pip` to the most updated version run the following.

        pip install --upgrade pip

6. Install dependencies with rosdep.

        sudo rosdep init
        rosdep update
        rosdep install --from-paths src -y --ignore-src
        
7. Install the CyberRunner packages.

        colcon build --symlink-install

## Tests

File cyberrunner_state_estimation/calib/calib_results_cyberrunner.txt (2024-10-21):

#polynomial coefficients for the DIRECT mapping function (ocam_model.ss in MATLAB). These are used by cam2world

5 -1.039121e+03 0.000000e+00 2.691087e-04 2.010848e-07 -7.252130e-11 

#polynomial coefficients for the inverse mapping function (ocam_model.invpol in MATLAB). These are used by world2cam

8 1591.697024 1225.708868 546.302676 502.415591 322.029177 256.157188 140.485896 29.168972 

#center: "row" and "column", starting from 0 (C convention)

614.883002 927.803988

#affine parameters "c", "d", "e"

1.000656 -0.000186 0.000525

#image size: "height" and "width"

1200 1920

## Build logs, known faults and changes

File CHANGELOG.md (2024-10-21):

# Change Log
 
## v0.1.0 (2024-10-21)
 
**Initial release.**

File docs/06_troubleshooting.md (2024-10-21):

Troubleshooting
=====

### Finding the center coordinate in OCamCalib is slow

See this [discussion](https://groups.google.com/g/ocamcalib-toolbox/c/ZgVP4LHd-6w).

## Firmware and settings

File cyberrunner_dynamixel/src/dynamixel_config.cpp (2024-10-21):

#include <stdio.h>
#include "dynamixel_sdk/dynamixel_sdk.h"

// ADDRESSES
#define ADDR_ID                 7
#define ADDR_BAUD_RATE          8
#define ADDR_OPERATING_MODE     11
#define ADDR_PROTOCOL_TYPE      13
#define ADDR_TEMPERATURE_LIMIT  31
#define ADDR_PWM_LIMIT          36
#define ADDR_SHUTDOWN           63
#define ADDR_VELOCITY_I		76
#define ADDR_VELOCITY_P		78

// VALUES
#define ID_1                    1
#define ID_2                    2
#define BAUD_RATE               3
#define OPERATING_MODE          0
#define PROTOCOL_TYPE           2
#define TEMPERATURE_LIMIT       70
#define PWM_LIMIT               666
#define SHUTDOWN                0x15
#define VELOCITY_I              400
#define VELOCITY_P              40


uint32_t baudrates[7] = {9600, 57600, 115200, 1000000, 2000000, 3000000, 4000000};


void configure_dynamixel(dynamixel::PortHandler* port_handler, dynamixel::PacketHandler* packet_handler, uint8_t dxl_id, uint8_t new_id)
{
    int dxl_comm_result;
    uint8_t dxl_error;

    // Set ID
    dxl_comm_result = packet_handler->write1ByteTxRx(port_handler, dxl_id, ADDR_ID, new_id, &dxl_error);
    if (dxl_comm_result != COMM_SUCCESS)
    {
        printf("Failed to set ID: %s\n", packet_handler->getTxRxResult(dxl_comm_result));
    }
    else if (dxl_error != 0)
    {
        printf("Error setting ID: %s\n", packet_handler->getRxPacketError(dxl_error));
    }
    else
    {
        printf("ID set to %d successfully\n", new_id);
    }

    // Set Baud Rate
    dxl_comm_result = packet_handler->write1ByteTxRx(port_handler, new_id, ADDR_BAUD_RATE, BAUD_RATE, &dxl_error);
    if (dxl_comm_result != COMM_SUCCESS)
    {
        printf("Failed to set Baud Rate: %s\n", packet_handler->getTxRxResult(dxl_comm_result));
    }
    else if (dxl_error != 0)
    {
        printf("Error setting Baud Rate: %s\n", packet_handler->getRxPacketError(dxl_error));
    }
    else
    {
        printf("Baud Rate set successfully\n");
    }

    // Set Operating Mode
    dxl_comm_result = packet_handler->write1ByteTxRx(port_handler, new_id, ADDR_OPERATING_MODE, OPERATING_MODE, &dxl_error);
    if (dxl_comm_result != COMM_SUCCESS)
    {
        printf("Failed to set Operating Mode: %s\n", packet_handler->getTxRxResult(dxl_comm_result));
    }
    else if (dxl_error != 0)
    {
        printf("Error setting Operating Mode: %s\n", packet_handler->getRxPacketError(dxl_error));
    }
    else
    {
        printf("Operating Mode set successfully\n");
    }

    // Set Protocol Type
    dxl_comm_result = packet_handler->write1ByteTxRx(port_handler, new_id, ADDR_PROTOCOL_TYPE, PROTOCOL_TYPE, &dxl_error);
    if (dxl_comm_result != COMM_SUCCESS)
    {
        printf("Failed to set Protocol Type: %s\n", packet_handler->getTxRxResult(dxl_comm_result));
    }
    else if (dxl_error != 0)
    {
        printf("Error setting Protocol Type: %s\n", packet_handler->getRxPacketError(dxl_error));
    }
    else
    {
        printf("Protocol Type set successfully\n");
    }

    // Set Temperature Limit
    dxl_comm_result = packet_handler->write1ByteTxRx(port_handler, new_id, ADDR_TEMPERATURE_LIMIT, TEMPERATURE_LIMIT, &dxl_error);
    if (dxl_comm_result != COMM_SUCCESS)
    {
        printf("Failed to set Temperature Limit: %s\n", packet_handler->getTxRxResult(dxl_comm_result));
    }
    else if (dxl_error != 0)
    {
        printf("Error setting Temperature Limit: %s\n", packet_handler->getRxPacketError(dxl_error));
    }
    else
    {
        printf("Temperature Limit set successfully\n");
    }

    // Set PWM Limit
    dxl_comm_result = packet_handler->write2ByteTxRx(port_handler, new_id, ADDR_PWM_LIMIT, PWM_LIMIT, &dxl_error);
    if (dxl_comm_result != COMM_SUCCESS)
    {
        printf("Failed to set PWM Limit: %s\n", packet_handler->getTxRxResult(dxl_comm_result));
    }
    else if (dxl_error != 0)
    {
        printf("Error setting PWM Limit: %s\n", packet_handler->getRxPacketError(dxl_error));
    }
    else
    {
        printf("PWM Limit set successfully\n");
    }

    // Set Shutdown value
    dxl_comm_result = packet_handler->write1ByteTxRx(port_handler, new_id, ADDR_SHUTDOWN, SHUTDOWN, &dxl_error);
    if (dxl_comm_result != COMM_SUCCESS)
    {
        printf("Failed to set Shutdown: %s\n", packet_handler->getTxRxResult(dxl_comm_result));
    }
    else if (dxl_error != 0)
    {
        printf("Error setting Shutdown: %s\n", packet_handler->getRxPacketError(dxl_error));
    }
    else
    {
        printf("Shutdown value set successfully\n");
    }

    // Set Velocity I Gain
    dxl_comm_result = packet_handler->write2ByteTxRx(port_handler, new_id, ADDR_VELOCITY_I, VELOCITY_I, &dxl_error);
    if (dxl_comm_result != COMM_SUCCESS)
    {
        printf("Failed to set Velocity I Gain: %s\n", packet_handler->getTxRxResult(dxl_comm_result));
    }
    else if (dxl_error != 0)
    {
        printf("Error setting Velocity I Gain: %s\n", packet_handler->getRxPacketError(dxl_error));
    }
    else
    {
        printf("Velocity I Gain set successfully\n");
    }

    // Set Velocity P Gain
    dxl_comm_result = packet_handler->write2ByteTxRx(port_handler, new_id, ADDR_VELOCITY_P, VELOCITY_P, &dxl_error);
    if (dxl_comm_result != COMM_SUCCESS)
    {
        printf("Failed to set Velocity P Gain: %s\n", packet_handler->getTxRxResult(dxl_comm_result));
    }
    else if (dxl_error != 0)
    {
        printf("Error setting Velocity P Gain: %s\n", packet_handler->getRxPacketError(dxl_error));
    }
    else
    {
        printf("Velocity P Gain set successfully\n");
    }
}

uint8_t scan_for_dynamixel(dynamixel::PortHandler* port_handler, dynamixel::PacketHandler* packet_handler)
{
    int dxl_comm_result;
    uint8_t dxl_error;
    uint8_t found_id = 0;

    for (uint8_t id = 1; id < 253; ++id)
    {
        dxl_comm_result = packet_handler->ping(port_handler, id, &dxl_error);
        if (dxl_comm_result == COMM_SUCCESS)
        {
            printf("Dynamixel with ID %d found\n", id);
            found_id = id;
            break;
        }
    }

    return found_id;
}

int main(int argc, char *argv[])
{
    // Get device
    const char* port = "/dev/ttyUSB0";
    if(argc >= 2) port = argv[1];
    printf("Using port: %s. Use the command-line argument to change the port, e.g.:\n  ros2 run cyberrunner_dynamixel dynamixel_config /dev/ttyUSB*\n", port);

    // Initialize PortHandler instance
    dynamixel::PortHandler *port_handler = dynamixel::PortHandler::getPortHandler(port);

    // Initialize PacketHandler instance
    dynamixel::PacketHandler *packet_handler = dynamixel::PacketHandler::getPacketHandler(PROTOCOL_TYPE);

    // Open port
    if (!port_handler->openPort())
    {
        printf("Failed to open the port!\n");
        return 0;
    }
    printf("Succeeded to open the port!\n");

    // Set port baudrate
    if (!port_handler->setBaudRate(1000000))
    {
        printf("Failed to change the baudrate!\n");
        return 0;
    }
    printf("Succeeded to change the baudrate!\n");

    printf("Plug in the Dynamixel to be assigned ID 1 [CONTROLS TILT OF LONGER EDGE OF MAZE] and press Enter...\n");
    getchar();  // Wait for user input

    // Scan for first Dynamixel
    uint8_t current_id = scan_for_dynamixel(port_handler, packet_handler);
    if (current_id == 0)
    {
        printf("No Dynamixel found. Please check the connection.\n");
        return 0;
    }

    // Configure first Dynamixel
    configure_dynamixel(port_handler, packet_handler, current_id, ID_1);

    printf("Unplug current Dynamixel and plug in the Dynamixel to be assigned ID 2 [CONTROLS TILT OF SHORTER EDGE OF MAZE] and press Enter...\n");
    getchar();  // Wait for user input

    // Scan for second Dynamixel
    current_id = scan_for_dynamixel(port_handler, packet_handler);
    if (current_id == 0)
    {
        printf("No Dynamixel found. Please check the connection.\n");
        return 0;
    }

    // Configure second Dynamixel
    configure_dynamixel(port_handler, packet_handler, current_id, ID_2);

    // Close port
    port_handler->closePort();

    return 0;
}

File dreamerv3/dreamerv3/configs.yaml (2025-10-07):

defaults:

  seed: 1
  method: name
  task: dummy_disc
  logdir: /dev/null
  replay: uniform
  replay_size: 1e6
  replay_online: False
  eval_dir: ''
  filter: '.*'

  jax:
    platform: gpu
    jit: True
    precision: float16
    prealloc: True
    debug_nans: False
    logical_cpus: 0
    debug: False
    policy_devices: [0]
    train_devices: [0]
    metrics_every: 10

  run:
    script: train
    steps: 1e10
    expl_until: 0
    log_every: 60
    save_every: 300
    eval_every: 1e6
    eval_initial: True
    eval_eps: 1
    eval_samples: 1
    train_ratio: 32.0
    train_fill: 0
    eval_fill: 0
    log_zeros: False
    log_keys_video: [image]
    log_keys_sum: '^$'
    log_keys_mean: '(log_entropy)'
    log_keys_max: '^$'
    from_checkpoint: ''
    sync_every: 1
    # actor_addr: 'tcp://127.0.0.1:5551'
    actor_addr: 'ipc:///tmp/5552'
    actor_batch: 32

  envs: {amount: 4, parallel: process, length: 0, reset: True, restart: True, discretize: 0, checks: False}
  wrapper: {length: 0, reset: True, discretize: 0, checks: False}
  env:
    atari: {size: [64, 64], repeat: 4, sticky: True, gray: False, actions: all, lives: unused, noops: 0, resize: opencv}
    dmlab: {size: [64, 64], repeat: 4, episodic: True}
    minecraft: {size: [64, 64], break_speed: 100.0}
    dmc: {size: [64, 64], repeat: 2, camera: -1}
    loconav: {size: [64, 64], repeat: 2, camera: -1}

  # Agent
  task_behavior: Greedy
  expl_behavior: None
  batch_size: 16
  batch_length: 64
  data_loaders: 8

  # World Model
  grad_heads: [decoder, reward, cont]
  rssm: {deter: 4096, units: 1024, stoch: 32, classes: 32, act: silu, norm: layer, initial: learned, unimix: 0.01, unroll: False, action_clip: 1.0, winit: normal, fan: avg}
  encoder: {mlp_keys: '.*', cnn_keys: '.*', act: silu, norm: layer, mlp_layers: 5, mlp_units: 1024, cnn: resnet, cnn_depth: 96, cnn_blocks: 0, resize: stride, winit: normal, fan: avg, symlog_inputs: True, minres: 4}
  decoder: {mlp_keys: '.*', cnn_keys: '.*', act: silu, norm: layer, mlp_layers: 5, mlp_units: 1024, cnn: resnet, cnn_depth: 96, cnn_blocks: 0, image_dist: mse, vector_dist: symlog_mse, inputs: [deter, stoch], resize: stride, winit: normal, fan: avg, outscale: 1.0, minres: 4, cnn_sigmoid: False}
  reward_head: {layers: 5, units: 1024, act: silu, norm: layer, dist: symlog_disc, outscale: 0.0, outnorm: False, inputs: [deter, stoch], winit: normal, fan: avg, bins: 255}
  cont_head: {layers: 5, units: 1024, act: silu, norm: layer, dist: binary, outscale: 1.0, outnorm: False, inputs: [deter, stoch], winit: normal, fan: avg}
  loss_scales: {image: 1.0, vector: 1.0, reward: 1.0, cont: 1.0, dyn: 0.5, rep: 0.1, actor: 1.0, critic: 1.0, slowreg: 1.0}
  dyn_loss: {impl: kl, free: 1.0}
  rep_loss: {impl: kl, free: 1.0}
  model_opt: {opt: adam, lr: 1e-4, eps: 1e-8, clip: 1000.0, wd: 0.0, warmup: 0, lateclip: 0.0}

  # Actor Critic
  actor: {layers: 5, units: 1024, act: silu, norm: layer, minstd: 0.1, maxstd: 1.0, outscale: 1.0, outnorm: False, unimix: 0.01, inputs: [deter, stoch], winit: normal, fan: avg, symlog_inputs: False}
  critic: {layers: 5, units: 1024, act: silu, norm: layer, dist: symlog_disc, outscale: 0.0, outnorm: False, inputs: [deter, stoch], winit: normal, fan: avg, bins: 255, symlog_inputs: False}
  actor_opt: {opt: adam, lr: 3e-5, eps: 1e-5, clip: 100.0, wd: 0.0, warmup: 0, lateclip: 0.0}
  critic_opt: {opt: adam, lr: 3e-5, eps: 1e-5, clip: 100.0, wd: 0.0, warmup: 0, lateclip: 0.0}
  actor_dist_disc: onehot
  actor_dist_cont: normal
  actor_grad_disc: reinforce
  actor_grad_cont: backprop
  critic_type: vfunction
  imag_horizon: 15
  imag_unroll: False
  horizon: 333
  return_lambda: 0.95
  critic_slowreg: logprob
  slow_critic_update: 1
  slow_critic_fraction: 0.02
  retnorm: {impl: perc_ema, decay: 0.99, max: 1.0, perclo: 5.0, perchi: 95.0}
  actent: 3e-4

  # Exploration
  expl_rewards: {extr: 1.0, disag: 0.1}
  expl_opt: {opt: adam, lr: 1e-4, eps: 1e-5, clip: 100.0, wd: 0.0, warmup: 0}
  disag_head: {layers: 5, units: 1024, act: silu, norm: layer, dist: mse, outscale: 1.0, inputs: [deter, stoch, action], winit: normal, fan: avg}
  disag_target: [stoch]
  disag_models: 8

cyberrunner:
  task: gym_cyberrunner_sim:cyberrunner-dreamer-v0
  envs.amount: 1
  replay: cyberrunner
  jax:
    logical_cpus: 8
  run:
    script: train
    train_ratio: 128
    actor_batch: 1
    save_every: 10
    log_keys_sum: '^log_reward$'
  encoder: {mlp_keys: 'states|goal$', cnn_keys: 'image'}
  decoder: {mlp_keys: 'states|goal$', cnn_keys: 'image'}
  wrapper: {length: 3000}

minecraft:

  task: minecraft_diamond
  envs.amount: 16
  run:
    script: train_save
    eval_fill: 1e5
    train_ratio: 16
    log_keys_max: '^log_inventory.*'
  encoder: {mlp_keys: 'inventory|inventory_max|equipped|health|hunger|breath|reward', cnn_keys: 'image'}
  decoder: {mlp_keys: 'inventory|inventory_max|equipped|health|hunger|breath', cnn_keys: 'image'}
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

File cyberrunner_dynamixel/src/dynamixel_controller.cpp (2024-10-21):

#include <fcntl.h>
#include <termios.h>
#include <stdlib.h>
#include <stdio.h>
#include <stdint.h>
#include <unistd.h>
#include <sys/time.h>
#include "dynamixel_sdk/dynamixel_sdk.h"

#include "cyberrunner_dynamixel/dynamixel_controller.h"
#include "cyberrunner_dynamixel/error_handling.h"

// Control table address, these might be different for different models.
#define ADDR_XL_TORQUE_ENABLE           64
#define ADDR_XL_PRESENT_VELOCITY        128
#define ADDR_XL_TEMPERATURE_LIMIT       31
#define ADDR_XL_PRESENT_POSITION        132
#define ADDR_XL_VELOCITY_KI             76
#define ADDR_XL_VELOCITY_KP             78
#define ADDR_XL_GOAL_CURRENT            102
#define ADDR_XL_GOAL_VELOCITY           104
#define ADDR_XL_HARDWARE_ERROR_STATUS   70  // Hardware error packet retrieval
#define ADDR_XL_PWM_OUTPUT              100 // Address for PWM output

// Protocol version
#define PROTOCOL_VERSION                2.0 // See which protocol version is used in the Dynamixel

#define XL_TEMPERATURE_LIMIT            50  // Maximum Temperature Allowable for Dynamixel
#define TORQUE_ENABLE                   1   // Value for enabling the torque
#define TORQUE_DISABLE                  0   // Value for disabling the torque
#define I_GAIN_VALUE                    400
#define P_GAIN_VALUE                    40

dynamixel::PortHandler *port_handler = NULL;
dynamixel::PacketHandler *packet_handler = NULL;

using namespace dynamixel;

int dynamixel_init(const char* port, int num_dynamixel, int* dynamixel_ids, int baudrate, uint16_t max_temp, uint32_t* positions)
{
    int dxl_comm_result = COMM_TX_FAIL;
    uint8_t dxl_error = 0;

    if(port_handler == NULL || packet_handler == NULL)
    {
        // Minimize latency on USB communication TODO: wrap in shell script
        char device[10];
        char cmd[256];
        sscanf(port, "/dev/%s", device);
        sprintf(cmd, "echo 1 | sudo tee /sys/bus/usb-serial/devices/%s/latency_timer", device);
        printf("Executing command: %s\n", cmd);
        system(cmd);

        // Initialize PortHandler Structs
        port_handler = PortHandler::getPortHandler(port);

        // Initialize PacketHandler Structs
        packet_handler = PacketHandler::getPacketHandler(PROTOCOL_VERSION);

        // Open port
        if (port_handler->openPort())
        {
            printf("Succeeded to open the port!\n");
        }
        else
        {
            printf("Failed to open the port!\n");
            return -1;
        }

        // Set port baudrate
        if (port_handler->setBaudRate(baudrate))
        {
            printf("Succeeded to change the baudrate!\n");
        }
        else
        {
            printf("Failed to change the baudrate!\n");
            return -1;
        }
    }

    for(int i = 0; i < num_dynamixel; i++)
    {
        // Dis- and enable Dynamixel Torque
        dxl_comm_result = packet_handler->write1ByteTxRx(port_handler, dynamixel_ids[i], ADDR_XL_TORQUE_ENABLE, TORQUE_DISABLE, &dxl_error);
        if (dxl_comm_result != COMM_SUCCESS)
        {
            printf("Failed to disable torque for Dynamixel ID %d: %s\n", dynamixel_ids[i], packet_handler->getTxRxResult(dxl_comm_result));
            return -1;
        }
        if (dxl_error != 0)
        {
            printf("Error disabling torque for Dynamixel ID %d: %s\n", dynamixel_ids[i], packet_handler->getRxPacketError(dxl_error));
            return -1;
        }

        dxl_comm_result = packet_handler->write1ByteTxRx(port_handler, dynamixel_ids[i], ADDR_XL_TORQUE_ENABLE, TORQUE_ENABLE, &dxl_error);
        if (dxl_comm_result != COMM_SUCCESS)
        {
            printf("Failed to enable torque for Dynamixel ID %d: %s\n", dynamixel_ids[i], packet_handler->getTxRxResult(dxl_comm_result));
            return -1;
        }
        if (dxl_error != 0)
        {
            printf("Error enabling torque for Dynamixel ID %d: %s\n", dynamixel_ids[i], packet_handler->getRxPacketError(dxl_error));
            return -1;
        }
        
        printf("Dynamixel (ID: %d) has been successfully connected \n", dynamixel_ids[i]);

        // Read present position
        dxl_comm_result = packet_handler->read4ByteTxRx(port_handler, dynamixel_ids[i], ADDR_XL_PRESENT_POSITION, (uint32_t*)&(positions[i]), &dxl_error);
        if (dxl_comm_result != COMM_SUCCESS)
        {
            printf("Failed to read present position for Dynamixel ID %d: %s\n", dynamixel_ids[i], packet_handler->getTxRxResult(dxl_comm_result));
            return -1;
        }
        if (dxl_error != 0)
        {
            printf("Error reading present position for Dynamixel ID %d: %s\n", dynamixel_ids[i], packet_handler->getRxPacketError(dxl_error));
            return -1;
        }
    }

    return 0;
}

void print_hardware_error_status(int dynamixel_id)
{
    uint8_t hardware_error_status = 0;
    uint8_t dxl_error = 0;
    int dxl_comm_result = packet_handler->read1ByteTxRx(port_handler, dynamixel_id, ADDR_XL_HARDWARE_ERROR_STATUS, &hardware_error_status, &dxl_error);

    if (dxl_comm_result != COMM_SUCCESS)
    {
        printf("Failed to read hardware error status for Dynamixel ID %d: %s\n", dynamixel_id, packet_handler->getTxRxResult(dxl_comm_result));
    }
    else if (dxl_error != 0)
    {
        printf("Hardware error status for Dynamixel ID %d: %s\n", dynamixel_id, packet_handler->getRxPacketError(dxl_error));
    }
    else
    {
        printf("Hardware error status for Dynamixel ID %d: 0x%02X\n", dynamixel_id, hardware_error_status);
    }
}
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
